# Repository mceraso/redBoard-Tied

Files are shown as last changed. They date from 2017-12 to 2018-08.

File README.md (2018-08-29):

# redBoard-Tied
Eagle Project to tie together redundant pins of the Sparkfun Quadstepper Motor Driver Board (the Red Board). When UNO Robotics first used the Red Board,
we realized quickly that we did not need all the pins available on the board. We wanted to save space on our Arduino, so we began to solder connections as pictured below.
After Sparkfun retired the Red Board, we were interested to see that they had left their designs open to the public. We wondered if we could continue making our own Red Boards while iterating on their design.
This project attempted to tie together the pins on the board that we used to solder by hand.

The first prototype failed in spectacular fashion as pictured below. We ordered our Red Board design from MacroFab with 1oz copper while Sparkfun's original design demanded 2oz copper. Because our prototpye had half as much copper as it needed, it could not handle the current, heated up quickly, and caught fire.

UNO Robotics has decided to put this project on hold due to the high cost of 2oz copper board fabrication and because the University of New Orleans has acquired its own PCB fabrication machine. As we improve in-house PCB fabrication ability, we intend to come back to the RedBoard project.

8.29.18: DEVELOPMENT IS BACK ON.
Because of our performance in the 2018 season, UNO Robotics has secured funding to move forward with a prototype of redBoard-Tied with 2oz copper. We're finalzing the parts list and will place an order with MacroFab soon.

# Original Red Board Front: 
Video Walkthough Front 

# Original Red Board Back:
Video Walkthough Back 

# How We Used to Tie the Board:
Video Walkthough Solder Tie 

# redBoard-Tied Front:
Video Walkthough Front 

# redBoard-Tied Back:
Video Walkthough Back 

# Prototype Front:
Video Walkthough Front 

# Prototype Back:
Video Walkthough Back 

# Helpful Links:
Quadstepper from SparkFun: https://www.sparkfun.com/products/retired/10507

Sparkfun's Quadstepper Repository: https://github.com/sparkfun/Quadstepper_Motor_Driver/tree/V_2.0.1

MacroFab: https://macrofab.com/

Eagle Tutorial from SparkFun: https://learn.sparkfun.com/tutorials/how-to-install-and-setup-eagle

UNO Robotics: http://www.uno.edu/student-involvement-leadership/orgs/robotics-club.aspx

GoFundMe: https://www.gofundme.com/unorobotics

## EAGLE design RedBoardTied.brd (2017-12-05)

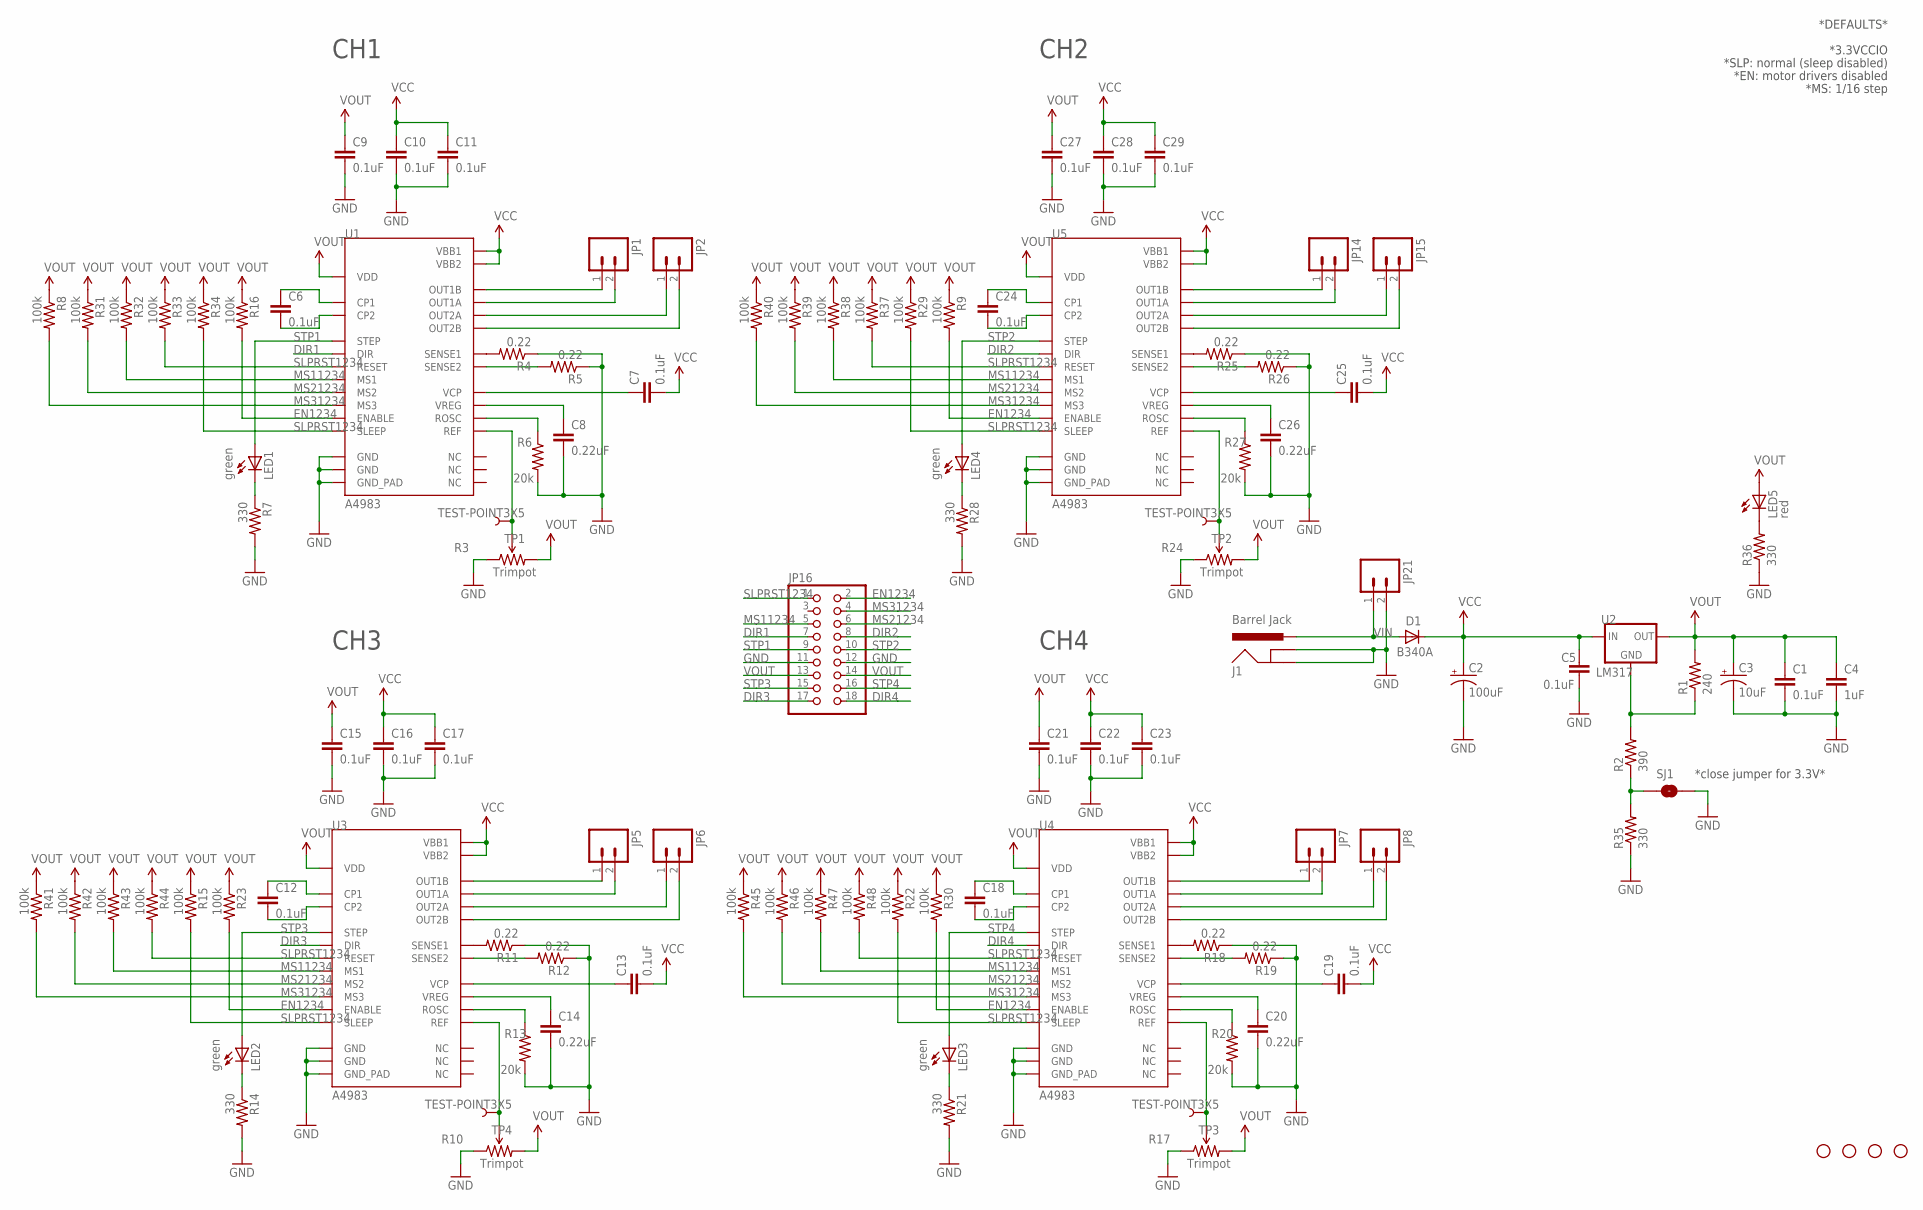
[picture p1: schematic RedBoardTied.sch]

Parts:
C1, C5, C6, C7, C9, C10, C11, C12, C13, C15, C16, C17, C18, C19, C21, C22, C23, C24, C25, C27, C28, C29: 0.1uF; 0402-CAP
C2: 100uF; PANASONIC_G
C3: 10uF; EIA3216
C4: 1uF; 0805
C8, C14, C20, C26: 0.22uF; 0402-CAP
D1: B340A; SMA-DIODE
J1: Barrel Jack; POWER_JACK_SMD
JP1, JP2, JP5, JP6, JP7, JP8, JP14, JP15: M023.5MM_LOCK; SCREWTERMINAL-3.5MM-2_LOCK
JP9, JP10, JP11, JP12: STAND-OFF
JP16: PINHD-2X9; 2X09
JP21: M02PTH; 1X02
LED1, LED2, LED3, LED4: green; LED-0603
LED5: red; LED-0603
R1: 240; 0402-RES
R2: 390; 0402-RES
R3, R10, R17, R24: Trimpot; TRIMPOT-3MM
R4, R5, R11, R12, R18, R19, R25, R26: 0.22; 0805
R6, R13, R20, R27: 20k; 0402-RES
R7, R14, R21, R28, R35, R36: 330; 0402-RES
R8, R9, R15, R16, R22, R23, R29, R30, R31, R32, R33, R34, R37, R38, R39, R40, R41, R42, R43, R44, R45, R46, R47, R48: 100k; 0402-RES
SJ1: SOLDERJUMPERNO; SJ_2S-NO
TP1, TP2, TP3, TP4: TEST-POINT3X5; PAD.03X.05
U1, U3, U4, U5: A4983; QFN-28-5MM
U2: LM317; DPAK

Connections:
DIR1: JP16.7, U1.P$19 (DIR)
DIR2: JP16.8, U5.P$19 (DIR)
DIR3: JP16.17, U3.P$19 (DIR)
DIR4: JP16.18, U4.P$19 (DIR)
EN1234: JP16.2, R9.2, R16.2, R23.2, R30.2, U1.P$2 (ENABLE), U3.P$2 (ENABLE), U4.P$2 (ENABLE), U5.P$2 (ENABLE)
GND: C1.2, C2.-, C3.C (-), C4.2, C5.2, C8.2, C9.2, C10.2, C11.2, C14.2, C15.2, C16.2, C17.2, C20.2, C21.2, C22.2, C23.2, C26.2, C27.2, C28.2, C29.2, J1.GND (GNDBREAK), J1.P$4 (GND), JP16.11, JP16.12, JP21.2, R3.1 (CCW), R4.1, R5.1, R6.2, R7.2, R10.1 (CCW), R11.1, R12.1, R13.2, R14.2, R17.1 (CCW), R18.1, R19.1, R20.2, R21.2, R24.1 (CCW), R25.1, R26.1, R27.2, R28.2, R35.1, R36.1, SJ1.2, U1.P$3 (GND), U1.P$18 (GND), U1.P$29 (GND_PAD), U3.P$3 (GND), U3.P$18 (GND), U3.P$29 (GND_PAD), U4.P$3 (GND), U4.P$18 (GND), U4.P$29 (GND_PAD), U5.P$3 (GND), U5.P$18 (GND), U5.P$29 (GND_PAD)
MS11234: JP16.5, R32.2, R38.2, R43.2, R47.2, U1.P$9 (MS1), U3.P$9 (MS1), U4.P$9 (MS1), U5.P$9 (MS1)
MS21234: JP16.6, R31.2, R39.2, R42.2, R46.2, U1.P$10 (MS2), U3.P$10 (MS2), U4.P$10 (MS2), U5.P$10 (MS2)
MS31234: JP16.4, R8.2, R40.2, R41.2, R45.2, U1.P$11 (MS3), U3.P$11 (MS3), U4.P$11 (MS3), U5.P$11 (MS3)
unnamed: R1.1, R2.2, U2.1 (GND)
unnamed: JP1.1, U1.P$21 (OUT1B)
unnamed: JP1.2, U1.P$24 (OUT1A)
unnamed: JP2.1, U1.P$26 (OUT2A)
unnamed: JP2.2, U1.P$1 (OUT2B)
unnamed: R4.2, U1.P$23 (SENSE1)
unnamed: R5.2, U1.P$27 (SENSE2)
unnamed: C7.1, U1.P$6 (VCP)
unnamed: C8.1, U1.P$8 (VREG)
unnamed: R6.1, U1.P$13 (ROSC)
unnamed: C6.1, U1.P$4 (CP1)
unnamed: R3.2 (WIPER), TP1.P$1, U1.P$17 (REF)
unnamed: C6.2, U1.P$5 (CP2)
unnamed: R11.2, U3.P$23 (SENSE1)
unnamed: LED1.C, R7.1
unnamed: R12.2, U3.P$27 (SENSE2)
unnamed: C13.1, U3.P$6 (VCP)
unnamed: C14.1, U3.P$8 (VREG)
unnamed: R13.1, U3.P$13 (ROSC)
unnamed: R10.2 (WIPER), TP4.P$1, U3.P$17 (REF)
unnamed: C12.1, U3.P$4 (CP1)
unnamed: R2.1, R35.2, SJ1.1
unnamed: C12.2, U3.P$5 (CP2)
unnamed: LED2.C, R14.1
unnamed: LED5.C, R36.2
unnamed: JP5.1, U3.P$21 (OUT1B)
unnamed: JP5.2, U3.P$24 (OUT1A)
unnamed: JP6.1, U3.P$26 (OUT2A)
unnamed: JP6.2, U3.P$1 (OUT2B)
unnamed: R18.2, U4.P$23 (SENSE1)
unnamed: R19.2, U4.P$27 (SENSE2)
unnamed: C19.1, U4.P$6 (VCP)
unnamed: C20.1, U4.P$8 (VREG)
unnamed: R20.1, U4.P$13 (ROSC)
unnamed: R17.2 (WIPER), TP3.P$1, U4.P$17 (REF)
unnamed: C18.1, U4.P$4 (CP1)
unnamed: C18.2, U4.P$5 (CP2)
unnamed: LED3.C, R21.1
unnamed: JP7.1, U4.P$21 (OUT1B)
unnamed: JP7.2, U4.P$24 (OUT1A)
unnamed: JP8.1, U4.P$26 (OUT2A)
unnamed: JP8.2, U4.P$1 (OUT2B)
unnamed: R25.2, U5.P$23 (SENSE1)
unnamed: R26.2, U5.P$27 (SENSE2)
unnamed: C25.1, U5.P$6 (VCP)
unnamed: C26.1, U5.P$8 (VREG)
unnamed: R27.1, U5.P$13 (ROSC)
unnamed: R24.2 (WIPER), TP2.P$1, U5.P$17 (REF)
unnamed: C24.1, U5.P$4 (CP1)
unnamed: C24.2, U5.P$5 (CP2)
unnamed: LED4.C, R28.1
unnamed: JP14.1, U5.P$21 (OUT1B)
unnamed: JP14.2, U5.P$24 (OUT1A)
unnamed: JP15.1, U5.P$26 (OUT2A)
unnamed: JP15.2, U5.P$1 (OUT2B)
SLPRST1234: JP16.1, R15.2, R22.2, R29.2, R33.2, R34.2, R37.2, R44.2, R48.2, U1.P$12 (RESET), U1.P$14 (SLEEP), U3.P$12 (RESET), U3.P$14 (SLEEP), U4.P$12 (RESET), U4.P$14 (SLEEP), U5.P$12 (RESET), U5.P$14 (SLEEP)
STP1: JP16.9, LED1.A, U1.P$16 (STEP)
STP2: JP16.10, LED4.A, U5.P$16 (STEP)
STP3: JP16.15, LED2.A, U3.P$16 (STEP)
STP4: JP16.16, LED3.A, U4.P$16 (STEP)
VCC: C2.+, C5.1, C7.2, C10.1, C11.1, C13.2, C16.1, C17.1, C19.2, C22.1, C23.1, C25.2, C28.1, C29.1, D1.C, U1.P$22 (VBB1), U1.P$28 (VBB2), U2.3 (IN), U3.P$22 (VBB1), U3.P$28 (VBB2), U4.P$22 (VBB1), U4.P$28 (VBB2), U5.P$22 (VBB1), U5.P$28 (VBB2)
VIN: D1.A, J1.VIN0 (PWR), JP21.1
VOUT: C1.1, C3.A (+), C4.1, C9.1, C15.1, C21.1, C27.1, JP16.13, JP16.14, LED5.A, R1.2, R3.3 (CW), R8.1, R9.1, R10.3 (CW), R15.1, R16.1, R17.3 (CW), R22.1, R23.1, R24.3 (CW), R29.1, R30.1, R31.1, R32.1, R33.1, R34.1, R37.1, R38.1, R39.1, R40.1, R41.1, R42.1, R43.1, R44.1, R45.1, R46.1, R47.1, R48.1, U1.P$15 (VDD), U2.4 (OUT), U3.P$15 (VDD), U4.P$15 (VDD), U5.P$15 (VDD)

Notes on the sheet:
CH1
CH2
CH3
CH4
*DEFAULTS*
*MS: 1/16 step
*3.3VCCIO
*close jumper for 3.3V*
*EN: motor drivers disabled
*SLP: normal (sleep disabled)

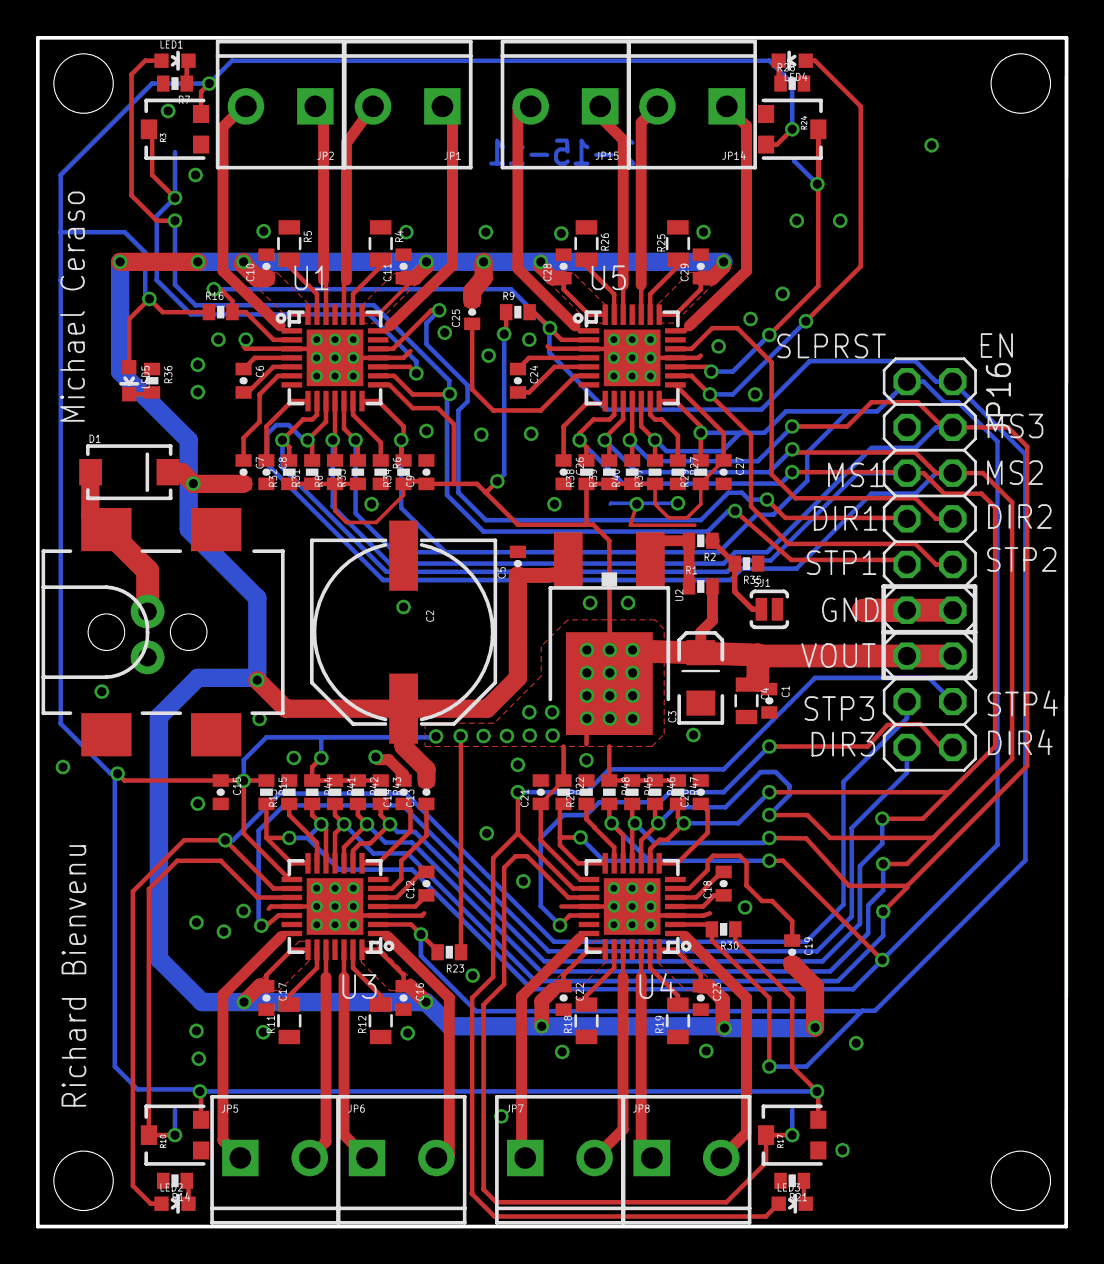
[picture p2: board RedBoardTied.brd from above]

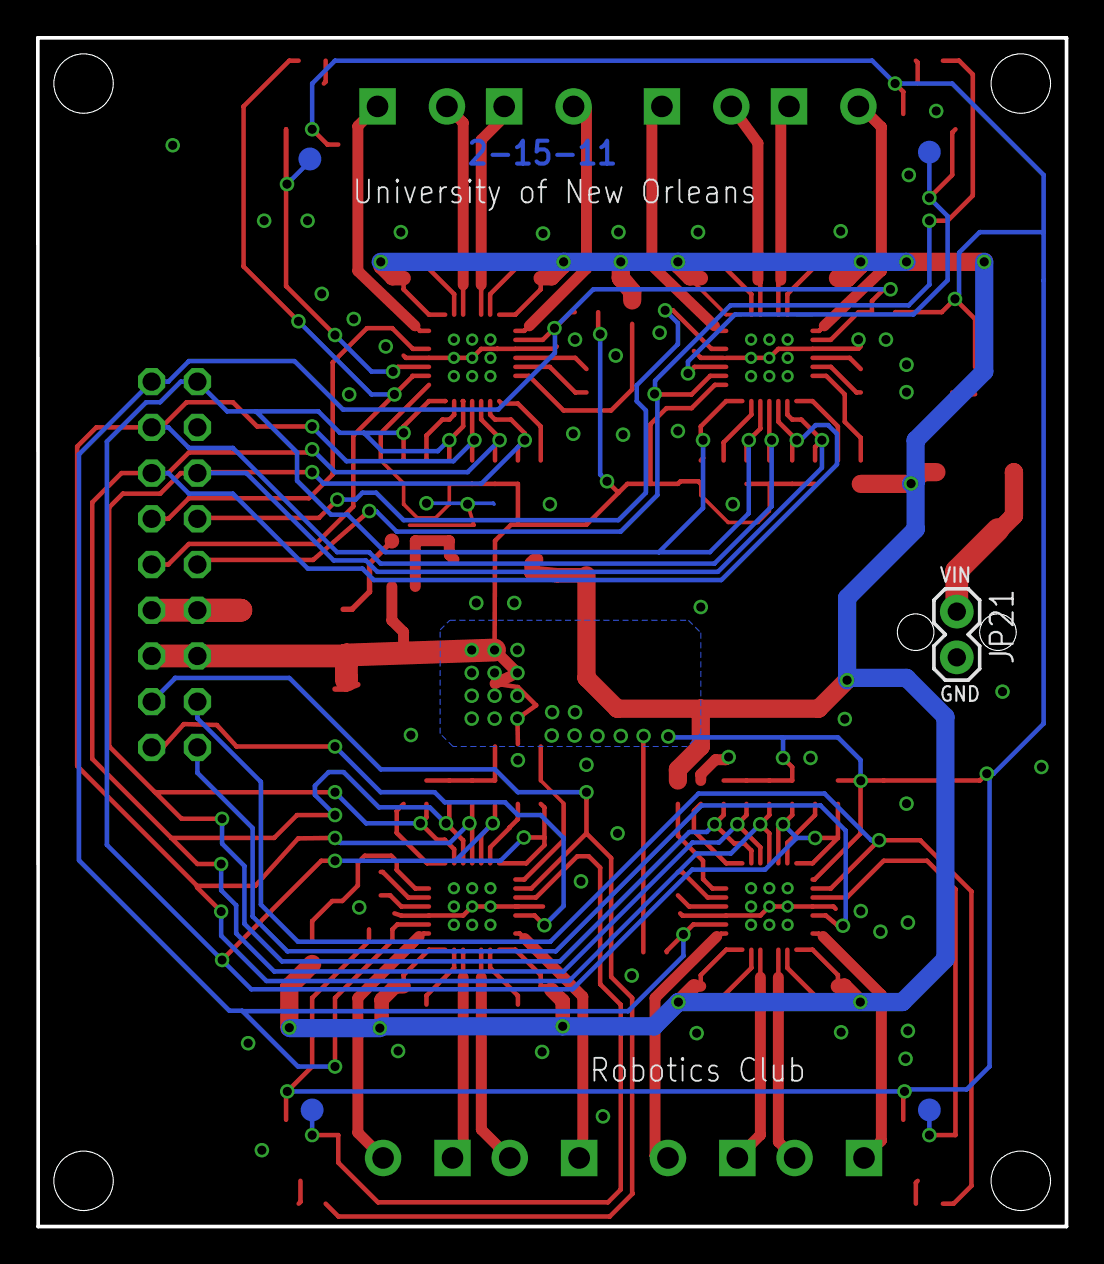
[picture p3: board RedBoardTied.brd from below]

Board: 2 copper layers, 57.1 x 66.0 mm, 108 parts (5 on the bottom side), 72 nets.
